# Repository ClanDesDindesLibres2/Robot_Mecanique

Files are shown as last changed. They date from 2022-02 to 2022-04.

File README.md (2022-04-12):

# Mechanics: Robotic arm and Chessboard
Our project aims to **create a robotic chess opponent**. <br> To achieve this, a unique chessboard and a robotic arm were designed. <br> The design of these two **MECHANICAL aspects** includes several **ELECTRICAL aspects** as well.
## Table of Contents
- [Robotic arm](https://github.com/ClanDesDindesLibres2/RoboticArm_ChessBoard_Mechanic#1--robotic-arm)
   - [Arm](https://github.com/ClanDesDindesLibres2/RoboticArm_ChessBoard_Mechanic#arm)
   - [Gripper](https://github.com/ClanDesDindesLibres2/RoboticArm_ChessBoard_Mechanic#gripper)
   - [Wooden Box](https://github.com/ClanDesDindesLibres2/RoboticArm_ChessBoard_Mechanic#wooden-box)
   - [Motors](https://github.com/ClanDesDindesLibres2/RoboticArm_ChessBoard_Mechanic/blob/main/README.md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)
- [Chess Board](https://github.com/ClanDesDindesLibres2/RoboticArm_ChessBoard_Mechanic#2--chessboard)
     - [Wooden Box](https://github.com/ClanDesDindesLibres2/RoboticArm_ChessBoard_Mechanic#wooden-box-1)
     - [Drawer](https://github.com/ClanDesDindesLibres2/RoboticArm_ChessBoard_Mechanic#drawer)
     - [Circuit of switches](https://github.com/ClanDesDindesLibres2/RoboticArm_ChessBoard_Mechanic#circuit-of-switches)
     - [Button and RGB led](https://github.com/ClanDesDindesLibres2/RoboticArm_ChessBoard_Mechanic#button-and-rgb-led)
## 1- Robotic arm
### 1.1- Mechanical parts of the robotic arm
#### Arm
The conception of the [robotic arm](https://github.com/ClanDesDindesLibres2/RoboticArm_ChessBoard_Mechanic/blob/main/Mechanical/Arm%20Solidworks/FULL_ASSEMBLY.SLDASM) is made in **SolidWorks**. <br>
Each part of the robotic arm is printed in plastic with a **3D printer**. <br>
Two different types of motors are used with this robotic arm. Both are **Dynamixel X-Series**, XL430-W250 and XM430-W350.
* All parts to print can be found in the [arm](https://github.com/ClanDesDindesLibres2/RoboticArm_ChessBoard_Mechanic/tree/main/Mechanical/Arm%20Solidworks/Bras-Robot) folder.
* To assemble the arm, follow the [instruction manual](https://github.com/ClanDesDindesLibres2/RoboticArm_ChessBoard_Mechanic/blob/main/Mechanical/Assembly_manual/Arm%20assembly%20and%20modification%20guide.pdf)
#### Gripper
The gripper is put at the end of the robotic arm. His purpose is to **pickup chess pieces**. <br>
The conception of the [gripper](https://github.com/ClanDesDindesLibres2/RoboticArm_ChessBoard_Mechanic/tree/main/Mechanical/Arm%20Solidworks/Bras-Robot/Gripper) is made in **SolidWorks**. <br>
Each part of the gripper is printed in plastic with a **3D printer**. <br>
The gripper uses one motor: a **servor motor**.
* All parts to print can be found in the [gripper](https://github.com/ClanDesDindesLibres2/RoboticArm_ChessBoard_Mechanic/tree/main/Mechanical/Arm%20Solidworks/Bras-Robot/Gripper) folder.
#### Wooden Box
* The pieces are cut from a 1/8 inch board with a laser cutter.
* The top and the sides of the box are cut with the file [WoodenBox_robot_base](https://github.com/ClanDesDindesLibres2/RoboticArm_ChessBoard_Mechanic/blob/main/Mechanical/WoodenBox/WoodenBox_robot_base.svg)
* The different pieces fit together and are glued together using wood glue 
### 1.2- Electrical parts of the robotic arm
#### Robot's motor 
The code for the motors is run in Arduino IDE and then executed with the OpenCR card. The Dynamixel Workbench library is needed to move the motors and the board OpenCR librairy is needed to convert the Arduino code to OpenCR. 
* Parts to acquire:
  * 2X motors: Dynamixels XM430-W350
  * 1X motor: Dynamixel 2XL430-W250

<br>These motors are part of the assemble guide linked above for the robotic arm.

## 2- Chessboard
### 2.1- Mechanical parts of the chessboard
#### Wooden Box
* The pieces are cut from a 1/4 inch board with a laser cutter.
* The top of the box is cut and engraved with the file [top](https://github.com/ClanDesDindesLibres2/RoboticArm_ChessBoard_Mechanic/blob/main/Mechanical/WoodenBox/top.svg).
* The top piece is then placed face down in the cutter to engrave the guide lines for the electrical diagram on the bottom of the [top](https://github.com/ClanDesDindesLibres2/RoboticArm_ChessBoard_Mechanic/blob/main/Mechanical/WoodenBox/top.svg) file. *OPTIONAL*
* The sides and the bottom are cut with the [sides](https://github.com/ClanDesDindesLibres2/RoboticArm_ChessBoard_Mechanic/blob/main/Mechanical/WoodenBox/sides.svg)  and [bottom](https://github.com/ClanDesDindesLibres2/RoboticArm_ChessBoard_Mechanic/blob/main/Mechanical/WoodenBox/bottom.svg)  files.
* The last part to this wooden box is a drawer. *ADDITIONAL*
* The front side of the wooden box must be remaid with the file [sides_tiroir_ext](https://github.com/ClanDesDindesLibres2/RoboticArm_ChessBoard_Mechanic/blob/main/Mechanical/WoodenBox/sides_tiroir_ext.svg).
* The following [instructions](https://github.com/ClanDesDindesLibres2/RoboticArm_ChessBoard_Mechanic/blob/main/README.md#drawer) explain the conception of the drawer inside the box.
* The different pieces fit together and are glued together using wood glue EXCEPT for the following:
   * The drawer door to the wooden box where it is written *Chess Bras*
   * The top of the box with the sides of the wooden box which allows access to the interior.
#### Drawer
* The pieces are cut from 1/8 inch board with a laser cutter.
* The drawer does not contain a top.
* The sides and the bottom of the drawer are cut with the file [sides_tiroir](https://github.com/ClanDesDindesLibres2/RoboticArm_ChessBoard_Mechanic/blob/main/Mechanical/WoodenBox/sides_tiroir.svg) and [fond_tiroir](https://github.com/ClanDesDindesLibres2/RoboticArm_ChessBoard_Mechanic/blob/main/Mechanical/WoodenBox/fond_tiroir.svg) respectively.
* All the pieces fit together and are glued with wood glue.
* The front of the drawer is glued to the interior of the outside face, [sides_tiroir_ext](https://github.com/ClanDesDindesLibres2/RoboticArm_ChessBoard_Mechanic/blob/main/Mechanical/WoodenBox/sides_tiroir_ext.svg), of the wooden box. 

### 2.2- Electrical parts of the chessboard
#### Circuit of switches
The circuit of switches is located below the top of the chessboard. To achieve this circuit some parts need to be bought.
* Parts to acquire:
  * 75 Switches: SWITCH REED SPST-N0 1A 125V, STANDEX-MEDER ELECTRONICS, SW GP560/15-20 AT
  * 100 Diodes: DIODE GEN PURP 400V 1A D041, DIODES INCORPORATED (VA)/ 1N4936-T
  * 32 Magnets 8mm dia.X 3mm
  * Glue gun
* To assemble the circuit, follow the electrical [plan](https://github.com/ClanDesDindesLibres2/RoboticArm_ChessBoard_Mechanic/tree/main/Electrical/Board)
#### Button and RGB LED
On the board, the led and the button can be found. The led is connected to the Pi and the button is connected to the Arduino.
* Parts to acquire:
  * LED RGB
  * Resistances: 2 X 100 Ohms & 1 X 200 Ohms
  * Miniature tactile switch 6X6X6mm

<br>The LED needs resistances. For the red one a 220 ohms, for the green one a 100 ohms and for the blue one a 100 ohms also is needed.
The LED's pins in the Rasberry Pi are 17 for the red one, 27 for the green one and 22 for the blue one.

<br>For further reference, an [image of the Raspberry Pi and it's installation](https://ozeki.hu/p_3047-how-to-setup-a-rgb-led-on-raspberry-pi.html) can be found.

## License
This project is licenced under a   license.

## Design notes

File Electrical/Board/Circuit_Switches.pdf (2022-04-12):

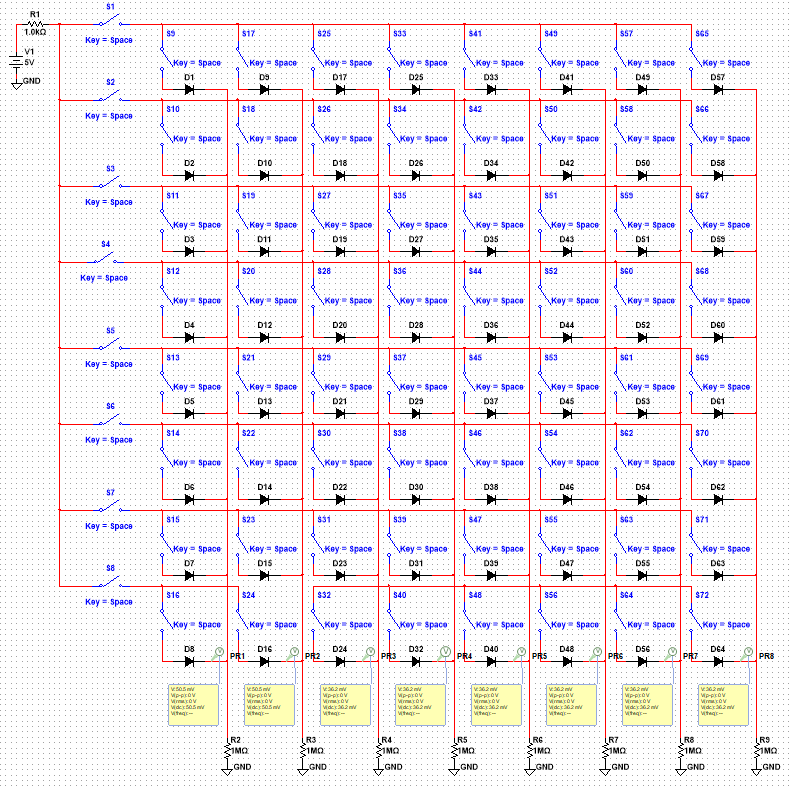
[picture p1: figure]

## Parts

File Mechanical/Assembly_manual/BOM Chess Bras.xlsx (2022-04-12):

No.article | Name of object | Desctription | Quantity
1 | dynamixel XM430-W350 | Motors for the arm | 2
2 | dynamixel 2XL430-W250 | Motors for the arm | 1
3 | d shaft 2in. | 2 inch long shaft | 1
4 | d shaft 4in. | 4 inch long shaft | 3
5 | Servo HS-422 | Servos for the gripper | 2
6 | Metal hub | hub for shaft | 9
7 | M2 2mm | M2 screw for dynamixels | 12
8 | M3 35mm | M3 for gripper | 3
9 | M3 40mm | M3 for gripper | 1
10 | M2 20mm | M2 for coupler and servos | 16
11 | M2 nut | Nut for coupler | 8
12 | S2 head 1/4 inch screw | Screw for wooden pieces | 8
13 | Dynamixels wire | To connect motors | 12
14 | dynamixels wires head | To connect wires | 8
15 | M2 10mm | To attach the servos | 8
16 | Robot base plate | 3D Printed | 1
17 | bearing support | 3D Printed | 1
18 | rotative plate | 3D Printed | 1
19 | inferior segment | 3D Printed | 1
20 | superior segment | 3D Printed | 1
21 | arm segement | 3D Printed | 1
22 | minisegment | 3D Printed | 1
23 | toppince | 3D Printed | 1
24 | gearmot | 3D Printed | 1
25 | gearnomot | 3D Printed | 1
26 | supportservo | 3D Printed | 1
27 | botsupp | 3D Printed | 1
28 | boutpince | 3D Printed | 2
29 | coupler 350w | 3D Printed | 2
30 | coupler 3 | 3D Printed | 1

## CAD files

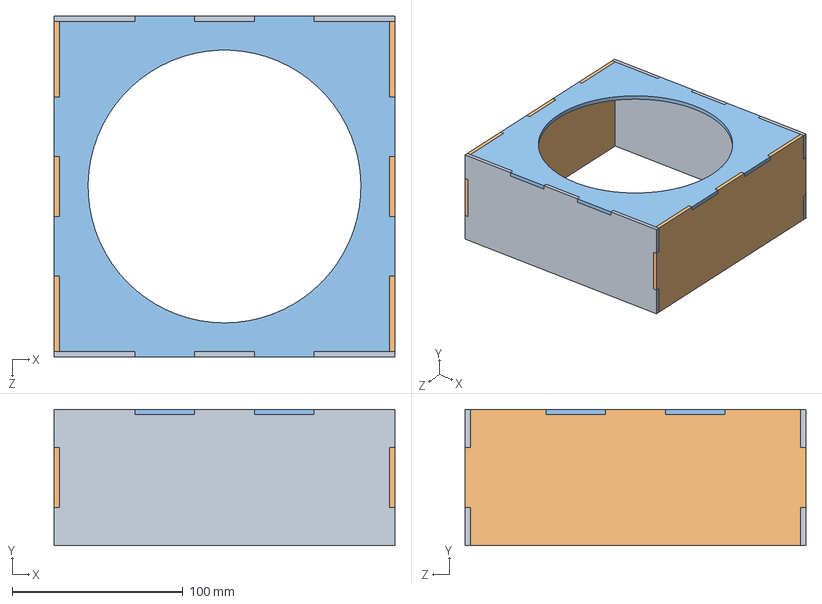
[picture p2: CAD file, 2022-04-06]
Mechanical/Arm Solidworks/Bras-Robot/Arm Box/ARM_BOX.SLDASM
200.0 x 80.0 x 200.0 mm
BOX_SIDE2 x 2
BOX_SIDE1 x 2
BOX_TOP

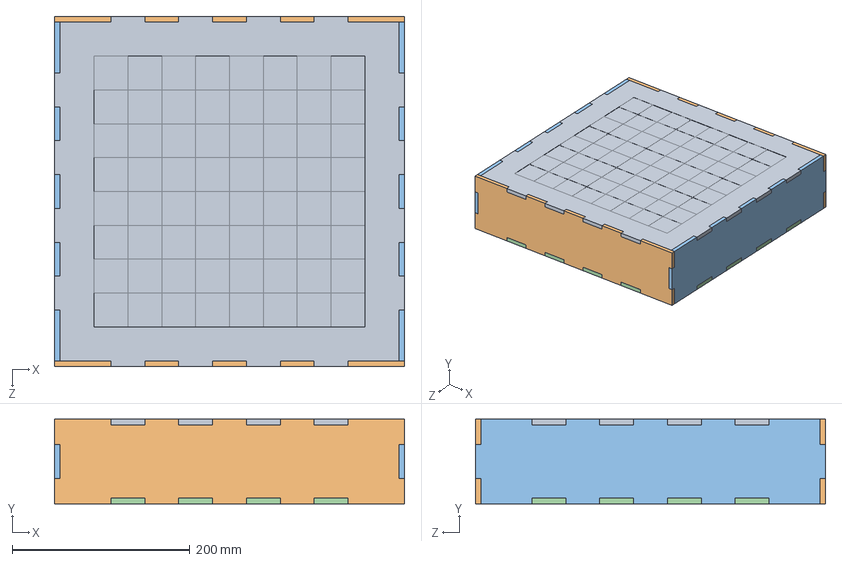
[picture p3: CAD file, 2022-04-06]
Mechanical/Arm Solidworks/Échiquier/CHESS_BOX.SLDASM
393.7 x 95.2 x 393.7 mm
TOP_BOX
BOX_SIDE_FRONT x 2
BOX_SIDE_LEFT_RIGTH x 2
BOTTOM_BOX

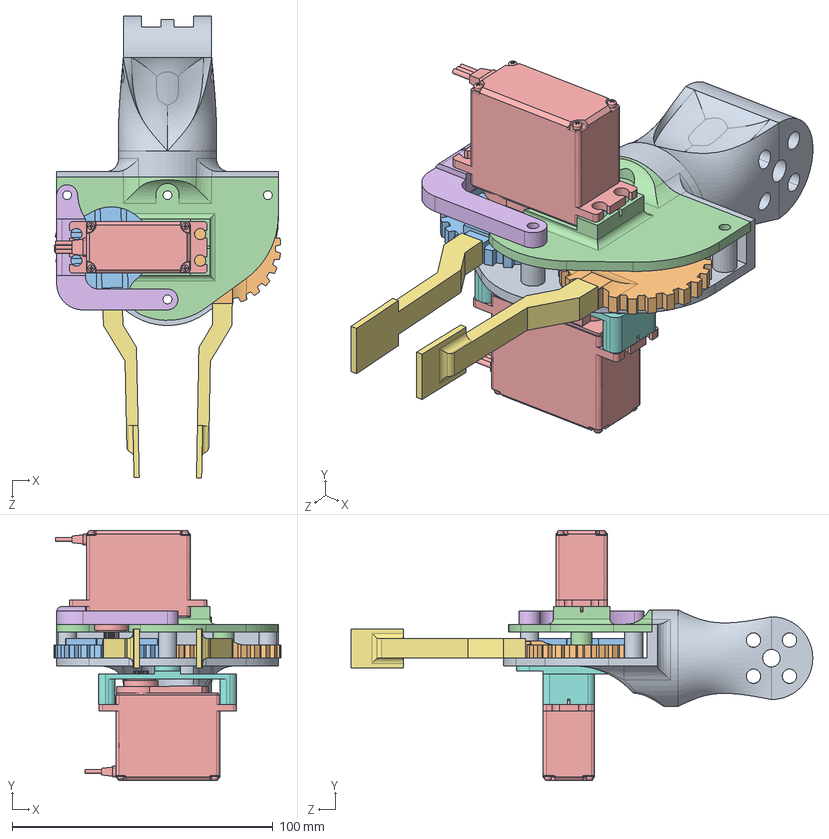
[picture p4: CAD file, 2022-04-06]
Mechanical/Arm Solidworks/Bras-Robot/Gripper/pince.SLDASM
86.9 x 95.9 x 177.1 mm
minisegmentServo
gearnoMot - Copie
gearMot
toppince
hs-422_sws x 2
supportServo
bout_pince x 2
BOTSUPP

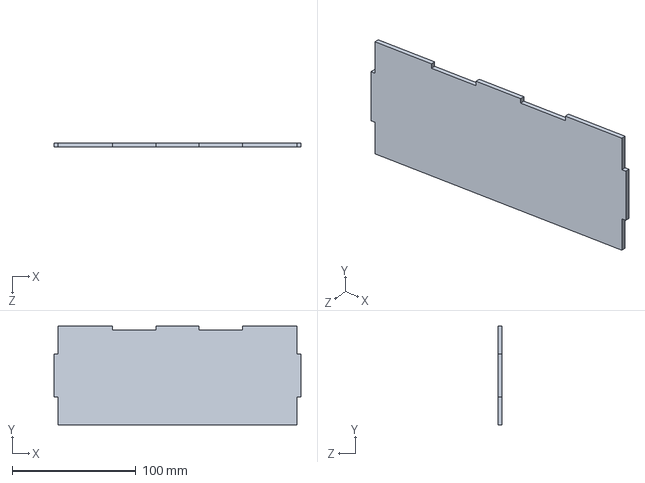
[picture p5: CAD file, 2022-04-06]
Mechanical/Arm Solidworks/Bras-Robot/Arm Box/BOX_SIDE1.SLDPRT
200.0 x 80.0 x 3.17 mm

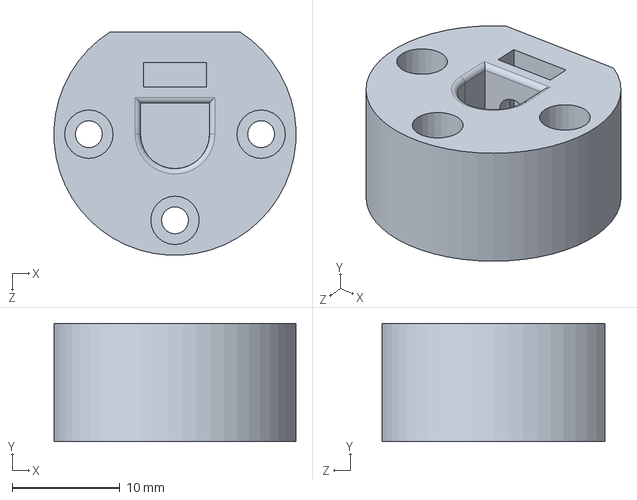
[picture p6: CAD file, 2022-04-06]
Mechanical/Arm Solidworks/Bras-Robot/Coupler/Coupler_Joint3.SLDPRT
22.5 x 11.0 x 20.7 mm

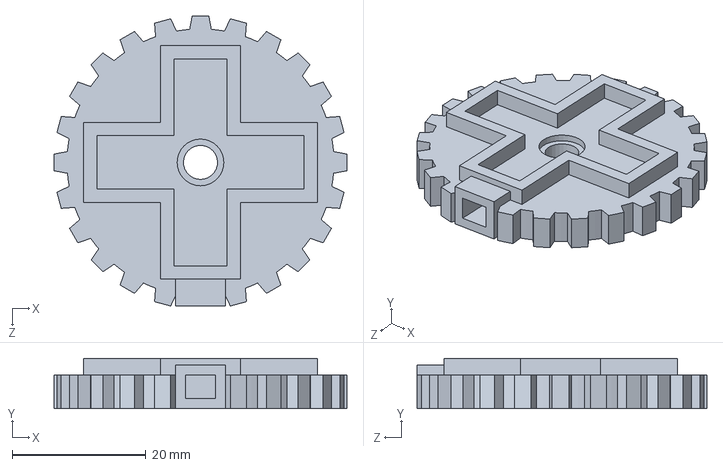
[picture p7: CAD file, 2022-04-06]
Mechanical/Arm Solidworks/Bras-Robot/Gripper/gearMot.SLDPRT
43.9 x 7.50 x 43.4 mm

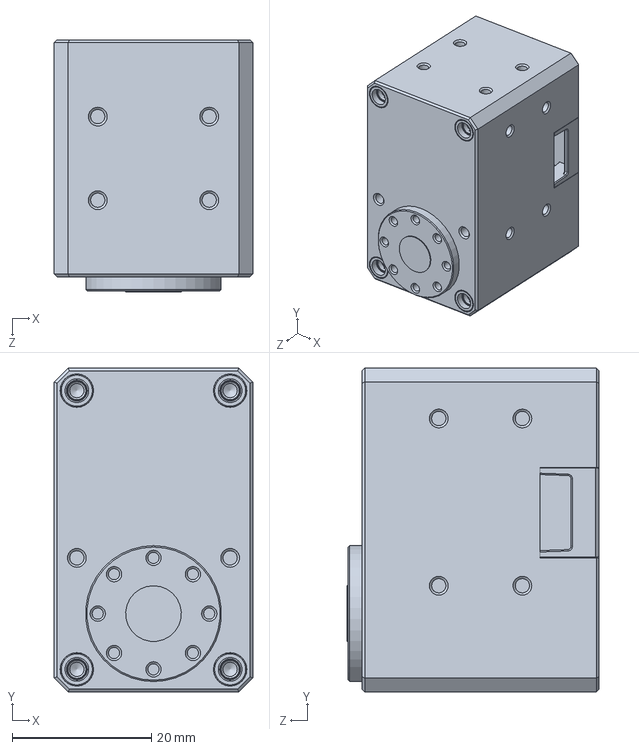
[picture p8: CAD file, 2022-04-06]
Mechanical/Arm Solidworks/Bras-Robot/Moteur/XL430-W250.SLDPRT
28.5 x 46.5 x 36.2 mm

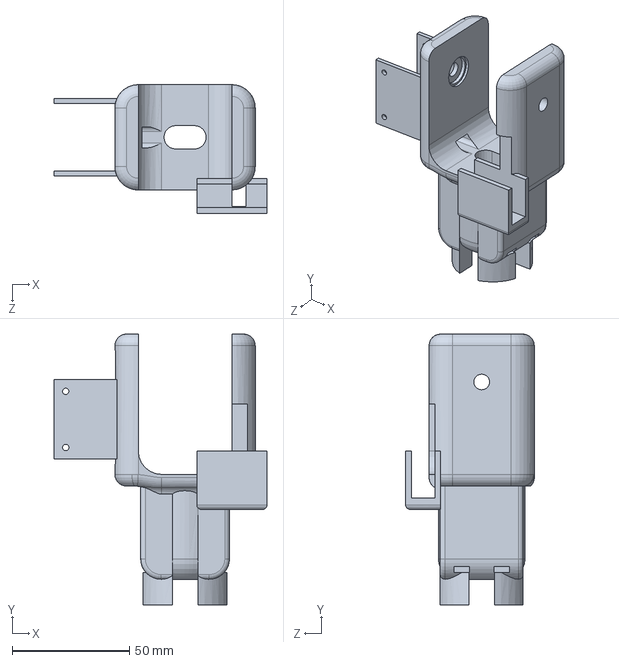
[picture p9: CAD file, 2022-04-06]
Mechanical/Arm Solidworks/Bras-Robot/wrist.SLDPRT
91.0 x 115.8 x 55.0 mm

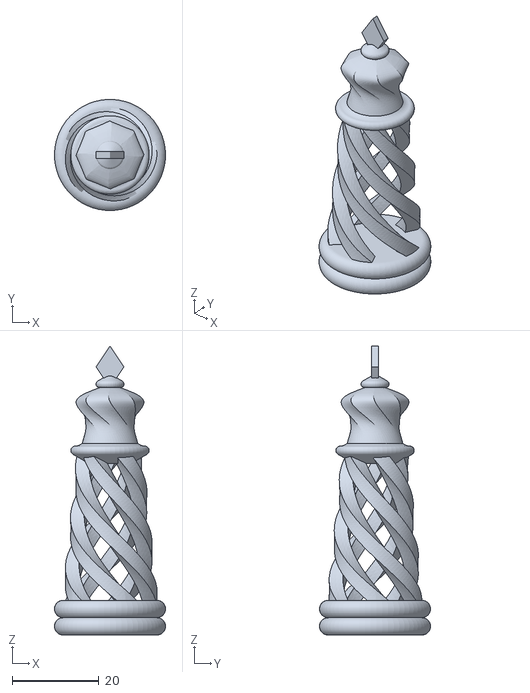
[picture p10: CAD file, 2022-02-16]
Mechanical/chess_pawn/KingV2.STL
25.6 x 25.6 x 66.6

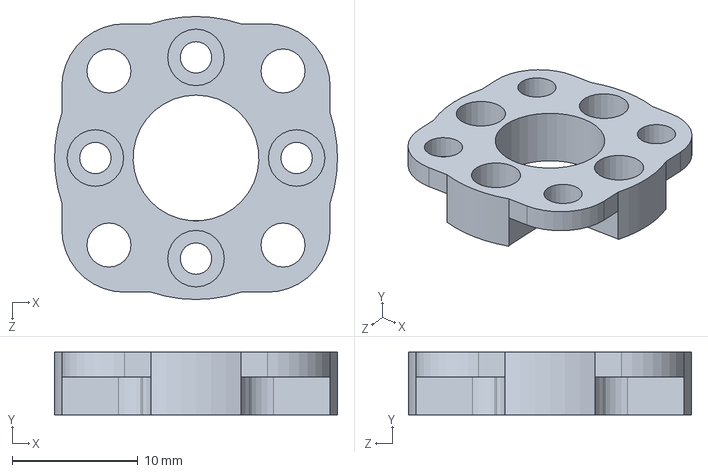
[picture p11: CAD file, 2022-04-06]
Mechanical/Arm Solidworks/Bras-Robot/Coupler/coupleur350W.SLDPRT
22.5 x 5.00 x 22.5 mm

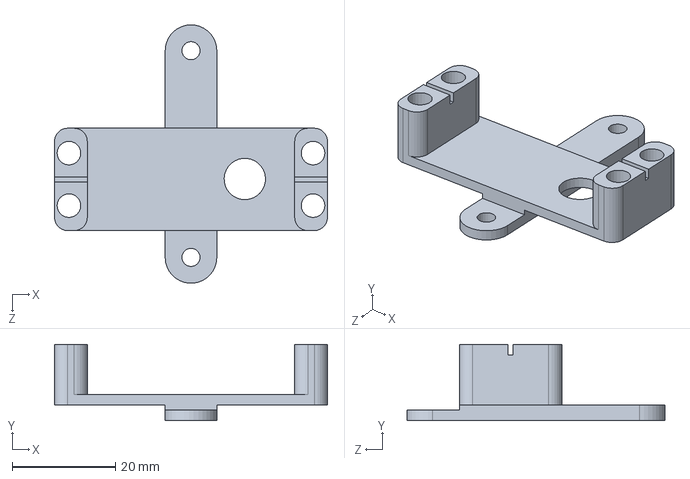
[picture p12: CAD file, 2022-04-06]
Mechanical/Arm Solidworks/Bras-Robot/Gripper/BOTSUPP.SLDPRT
52.8 x 14.7 x 50.0 mm

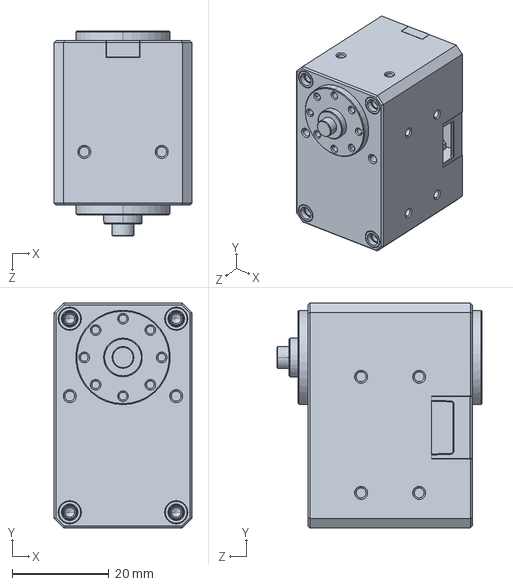
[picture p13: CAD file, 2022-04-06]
Mechanical/Arm Solidworks/Bras-Robot/Moteur/XM430-W350.SLDPRT
28.5 x 46.5 x 42.4 mm

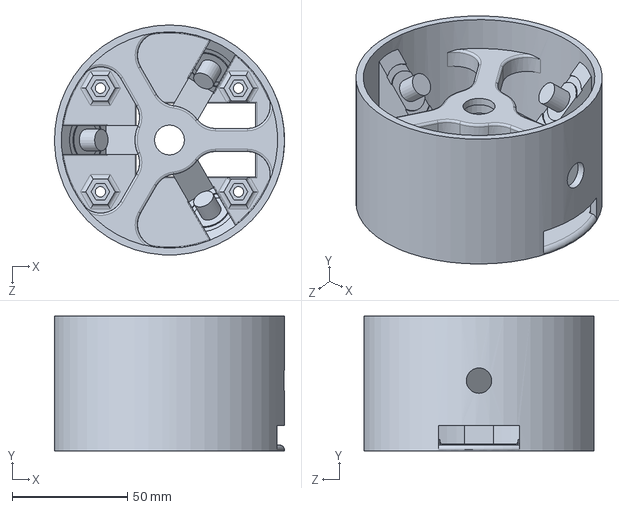
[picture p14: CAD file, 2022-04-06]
Mechanical/Arm Solidworks/Bras-Robot/Support_Bearing_V4.SLDPRT
100.0 x 58.5 x 100.0 mm

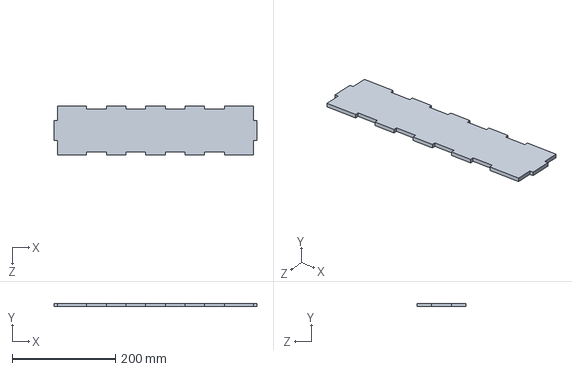
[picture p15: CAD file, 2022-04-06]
Mechanical/Arm Solidworks/Échiquier/BOX_SIDE_LEFT_RIGTH.SLDPRT
393.7 x 6.35 x 95.2 mm

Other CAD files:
Mechanical/Arm Solidworks/Échiquier/arm_box.SLDPRT
Mechanical/chess_pawn/BishopV2.STL
Mechanical/Arm Solidworks/Bras-Robot/Arm Box/BOX_TOP.SLDPRT
Mechanical/Arm Solidworks/Bras-Robot/base_robot.SLDPRT
Mechanical/Arm Solidworks/Bras-Robot/Arm Box/BOX_SIDE2.SLDPRT
Mechanical/Arm Solidworks/Bras-Robot/Gripper/bout_pince.SLDPRT
Mechanical/Arm Solidworks/Bras-Robot/Gripper/gearnoMot - Copie.SLDPRT
Mechanical/Arm Solidworks/Bras-Robot/Gripper/hs-422_sws.SLDPRT
Mechanical/Arm Solidworks/Bras-Robot/Gripper/minisegmentServo.SLDPRT
Mechanical/Arm Solidworks/Bras-Robot/Gripper/supportServo.SLDPRT
Mechanical/Arm Solidworks/Bras-Robot/Gripper/toppince.SLDPRT
Mechanical/Arm Solidworks/Bras-Robot/Others/545548_hub.SLDASM
Mechanical/Arm Solidworks/Bras-Robot/Others/M2-4mm_TYPE 18-8 SS SOCKET HEAD CAP SCREW.SLDPRT
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

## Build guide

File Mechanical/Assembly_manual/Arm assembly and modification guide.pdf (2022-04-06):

Assembly and modification guide to the Chess-Bras’s robotic arm.

The robotic arm for the Chess-Bras project is a derivation of the Handling-Gro’s robot project. Some modifications have been made to suite our needs. This guide explain how we assemble our arm, the modifications we had to the original project and what modification to our robot we would’ve done to perfect the arm with more time.

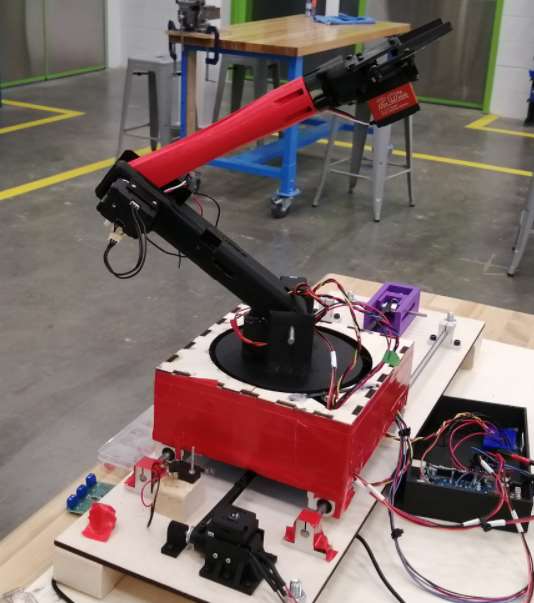
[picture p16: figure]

Figure 1 : Handling-Gro Project

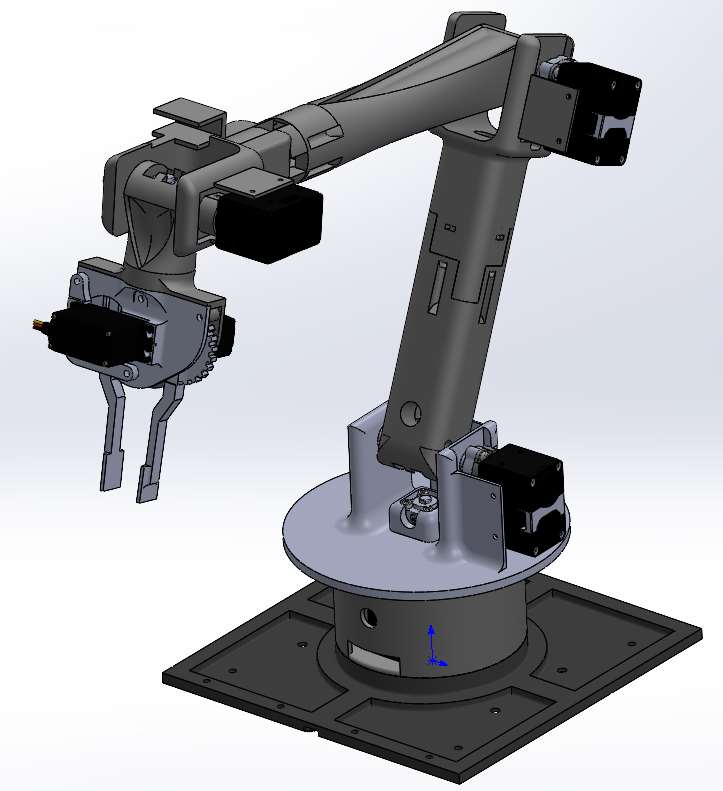
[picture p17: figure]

Figure 2 : Chess-Bras' arm
The main difference between the original and our version is the removal of the linear joint at the bottom, the addition of a 4th joint at the end of the arm and the simplification of the gripper.

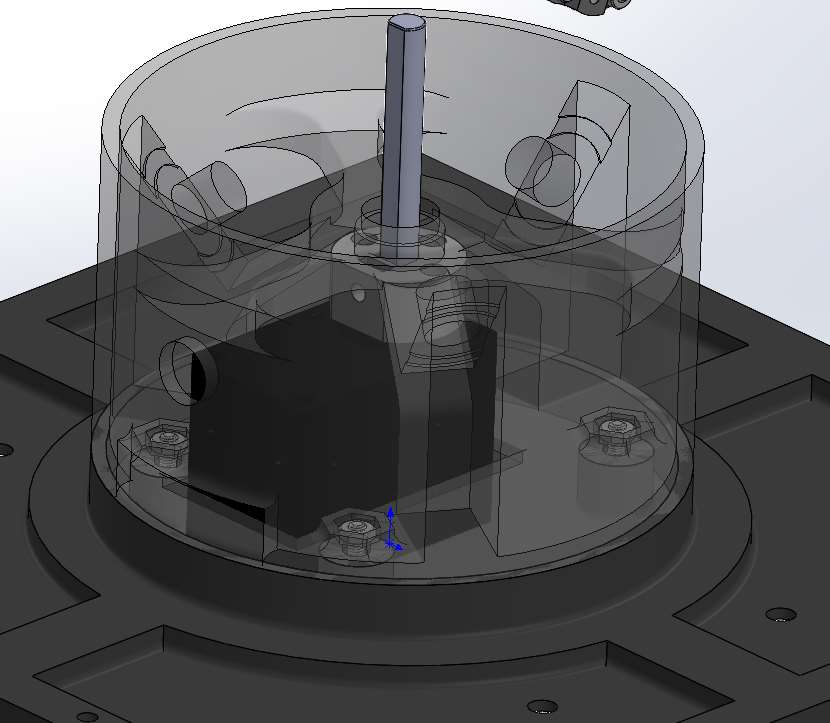
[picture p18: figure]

- To assemble the base, you must connect the first motor and screw it in with the coupler and the shaft. After you screw the support bearing.

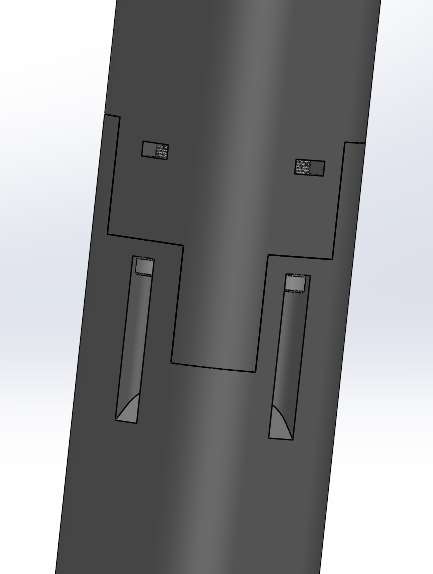
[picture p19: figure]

- The fit between the superior and inferior segment is pretty thigh. We only put 2 screws in and without the nut in the hole planned for it. It is strong enough because there is not a lot of tension in this section.

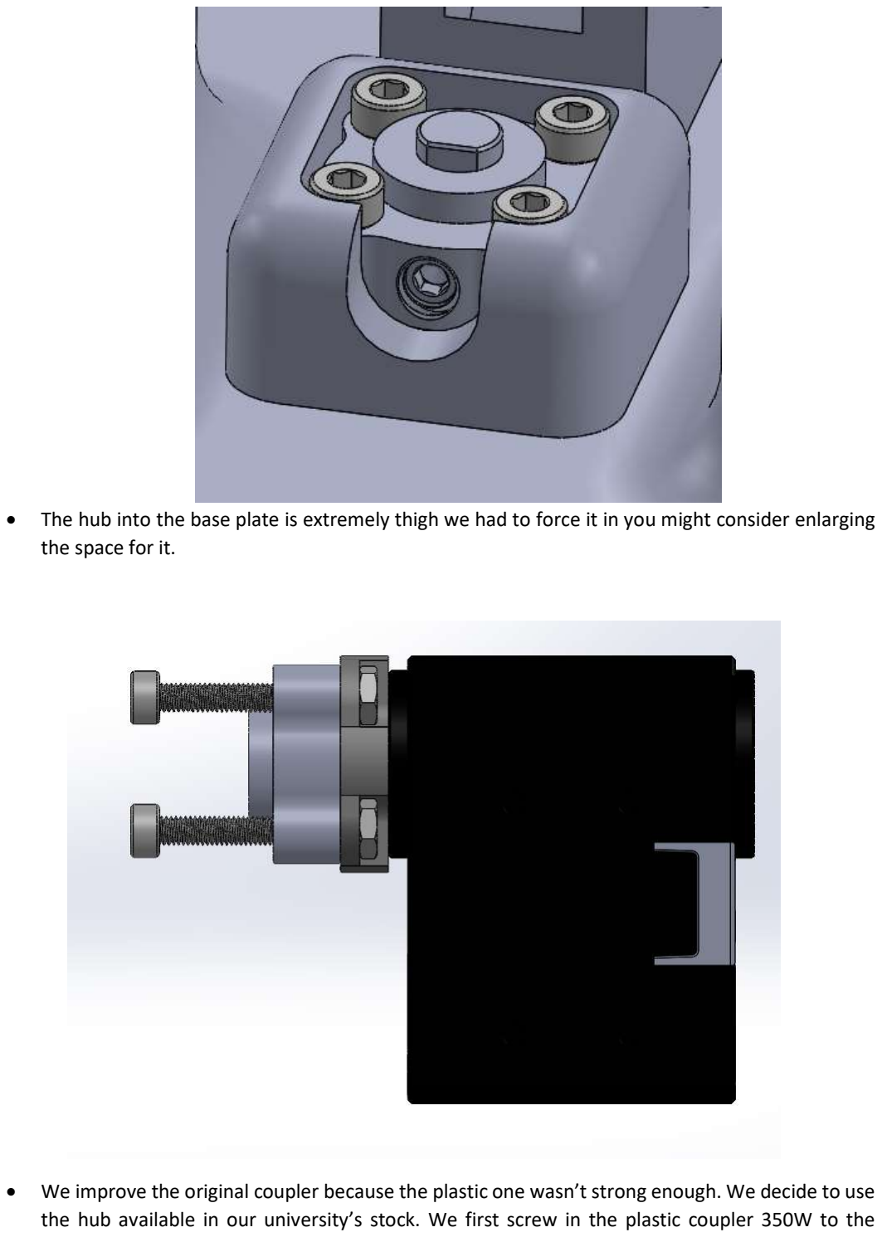
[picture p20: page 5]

- The hub into the base plate is extremely thigh we had to force it in you might consider enlarging the space for it.
- We improve the original coupler because the plastic one wasn’t strong enough. We decide to use the hub available in our university’s stock. We first screw in the plastic coupler 350W to the

Dynamixel. After, we insert smaller screws (M2) than the hub hole and we fix it with the nut. This assembly is strong enough the pieces that are most likely to fail is the small screws between the motor and the plastic coupler.

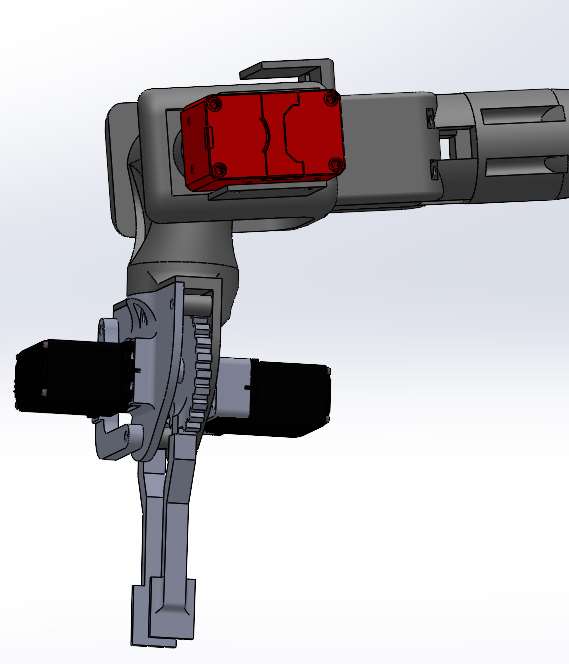
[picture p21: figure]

- In our research we realize that the OpenCr card cannot support 4 Dynamixels due to the lack of current output. We decide to remove the last motor and make the gripper free of movement. To balance the gripper to a vertical position, we put 2 servos on the gripper on for the gripper action and one as a counterweight. With more time, we would’ve found a way to connect the last motor. Problems we had in the assembly.
- The gear in the gripper and their axles needed to be sanded to have good movement.
- The support bearing was extremely sanded to fit with the base plate. The 3 bearings are useless. It will be a good idea to change the first joint contact. With an axial bearing or something else.
- The base plate is flexible we add a ¼ inch wooden plate for weight and solidity.
- The assembly use a lot of types of screws. It will be useful to either only use a metric or imperial set of screws.
